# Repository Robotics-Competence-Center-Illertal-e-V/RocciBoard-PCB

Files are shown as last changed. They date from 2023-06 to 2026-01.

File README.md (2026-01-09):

# Rocci Board

# Features

* 4x DC Motor outputs a 3 A (motor driver with current limitation)
* 8 separate i2c channels
* low voltage shutdown for battery protection
* i2c fully protected against 12V and reverse polarity
* 3 A switching regulator for 5 V
* 3,3 V with 1 A LDO
* 8 V for Arduino VIN pin
* reverse polarity protection on battery connector
* short circuit protection on all supply pins

# Schematic

[Schematic as pdf](documentation/RocciBoard.pdf)

[Layout as pdf](documentation/RocciBoard__Assembly.pdf)

# Pinout Diagram

## Top

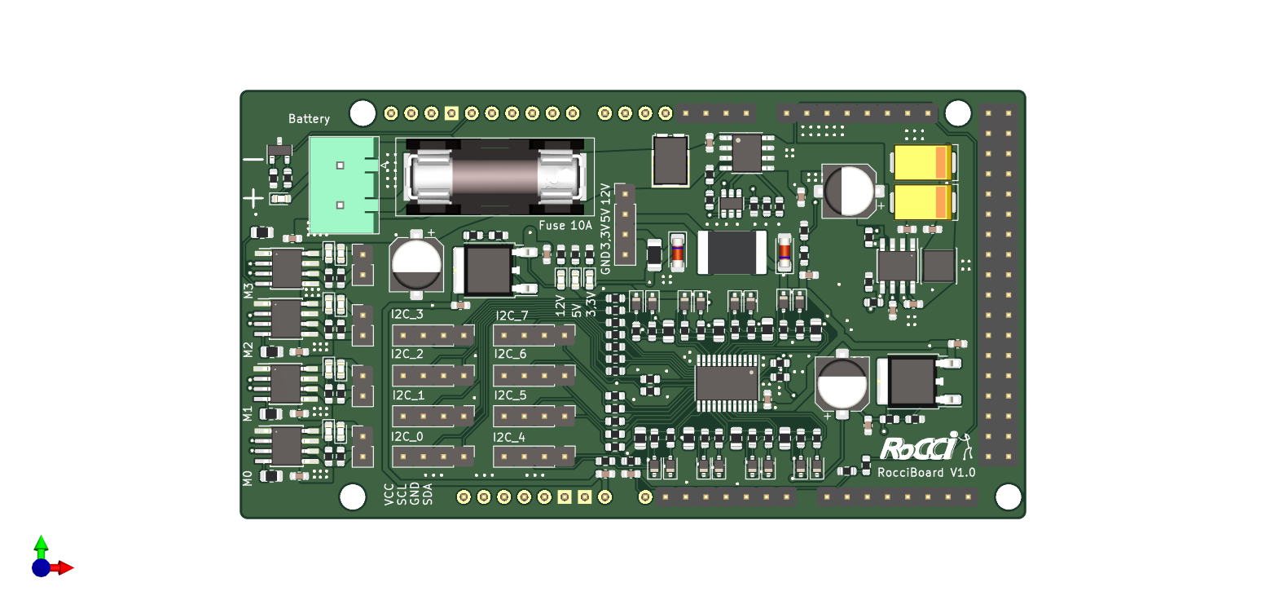
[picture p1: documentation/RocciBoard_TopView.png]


## Bottom

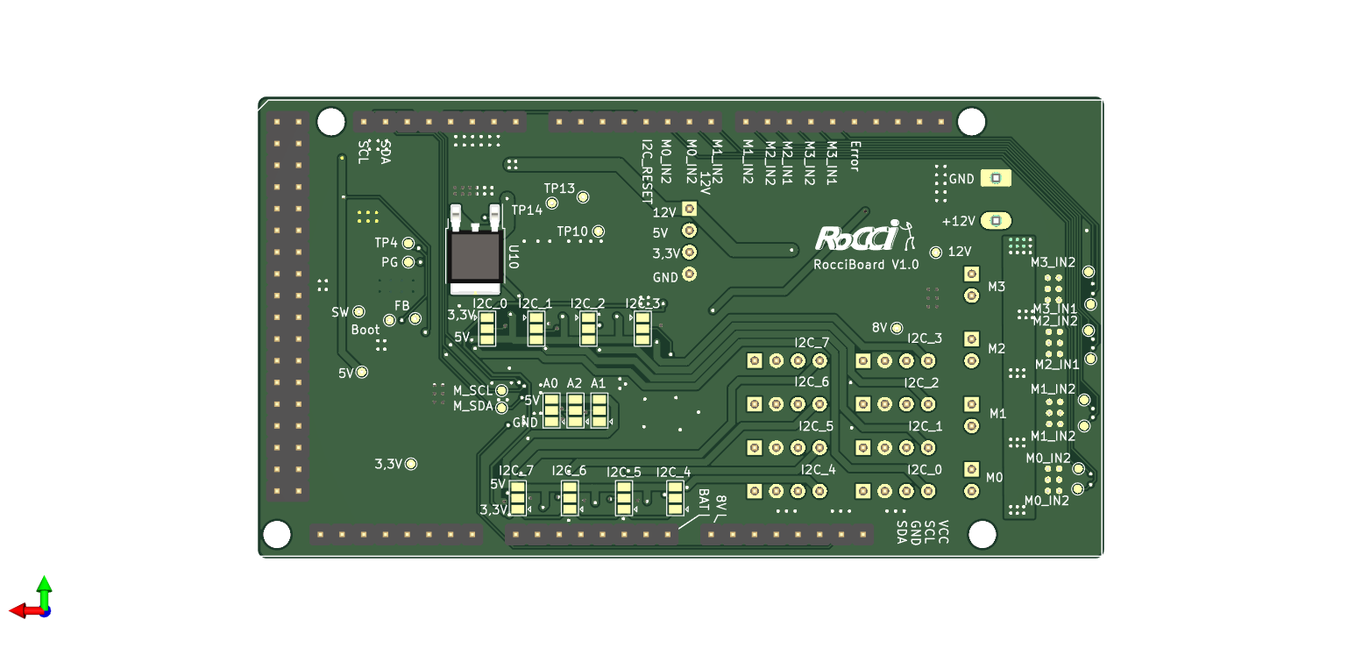
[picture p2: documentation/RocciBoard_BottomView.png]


## Hand Assembled Components

male pinheader with femal back:
1* 4
1* 7
2* 8
1* 18x2

male pinheader:
1* 8
1* 10
1* 4
1* 1
9* 4
4* 2

1* XT60 Male

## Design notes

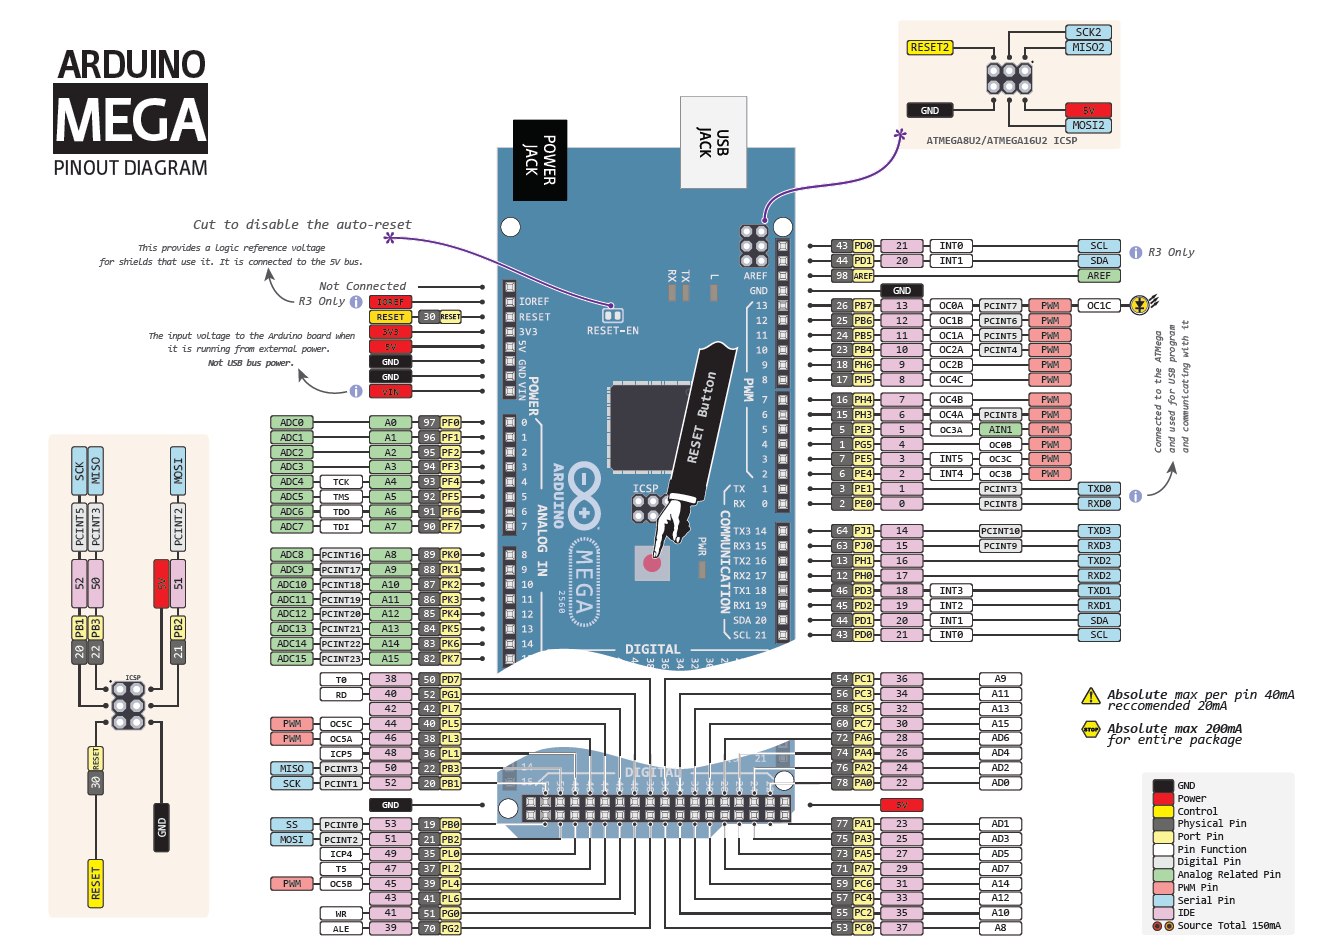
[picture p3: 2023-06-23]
datasheets/ARDUINO-Mega-Pinout-Diagram.png

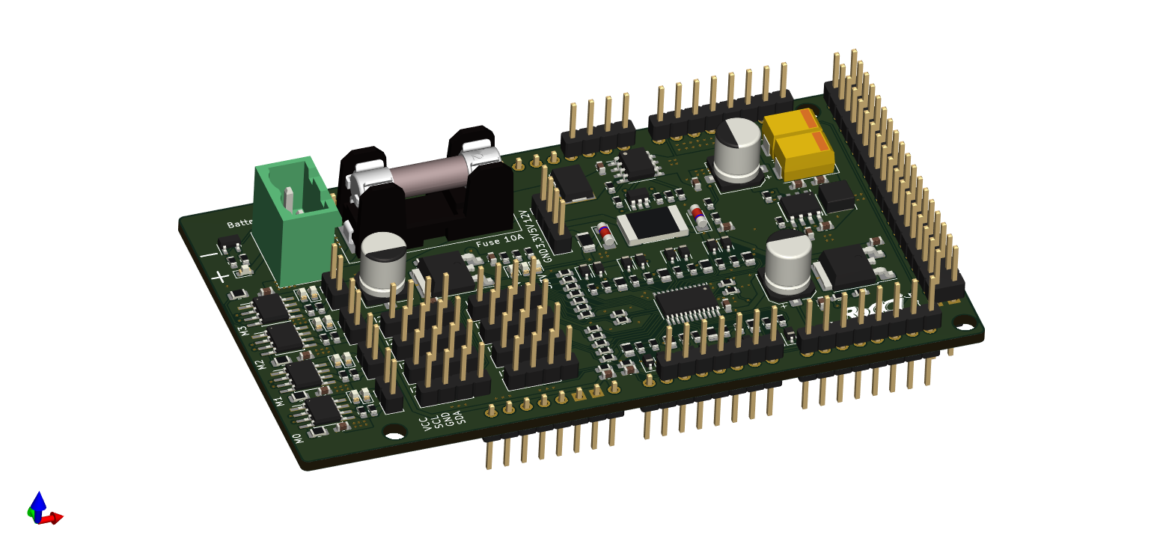
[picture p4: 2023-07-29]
documentation/RocciBoard_3DView.png

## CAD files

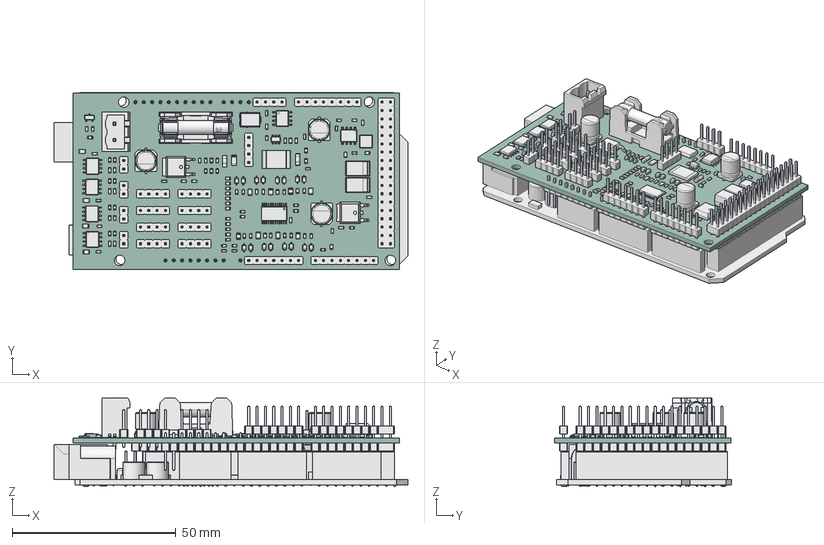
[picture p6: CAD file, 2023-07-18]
3d_model/board_arduino_assembly.FCStd
108.0 x 54.0 x 27.0 mm
ArduinoMega_STEP_AP203
RocciShield PCB

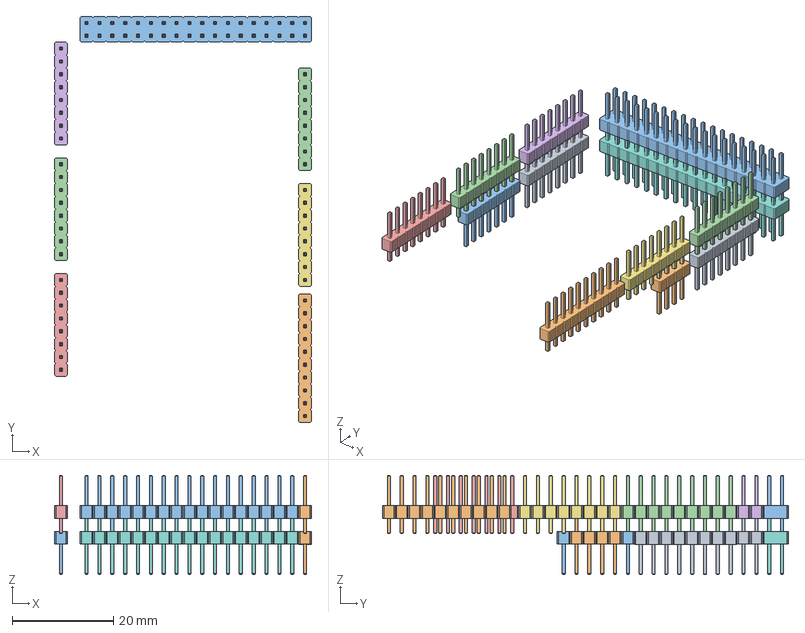
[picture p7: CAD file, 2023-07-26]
custom_parts/3d_shield_connector.FCStd
50.8 x 80.3 x 19.6 mm
PinHeader_1x08_P254mm_Vertical
PinHeader_1x10_P254mm_Vertical
PinHeader_2x18_P254mm_Vertical
PinHeader_1x08_P254mm_Vertical001
PinHeader_1x08_P254mm_Vertical002
PinHeader_1x08_P254mm_Vertical003
PinHeader_1x08_P254mm_Vertical004
PinHeader_2x18_P254mm_Vertical001
PinHeader_1x08_P254mm_Vertical005
PinHeader_1x04_P254mm_Vertical
PinHeader_1x07_P254mm_Vertical
PinHeader_1x08_P254mm_Vertical006

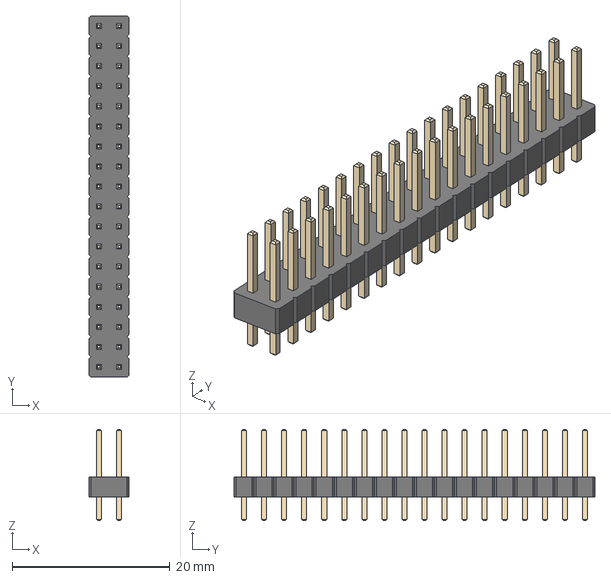
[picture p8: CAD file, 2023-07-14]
external_libs/PinHeader_2x18_P2.54mm_Vertical.step
5.08 x 45.7 x 11.5 mm

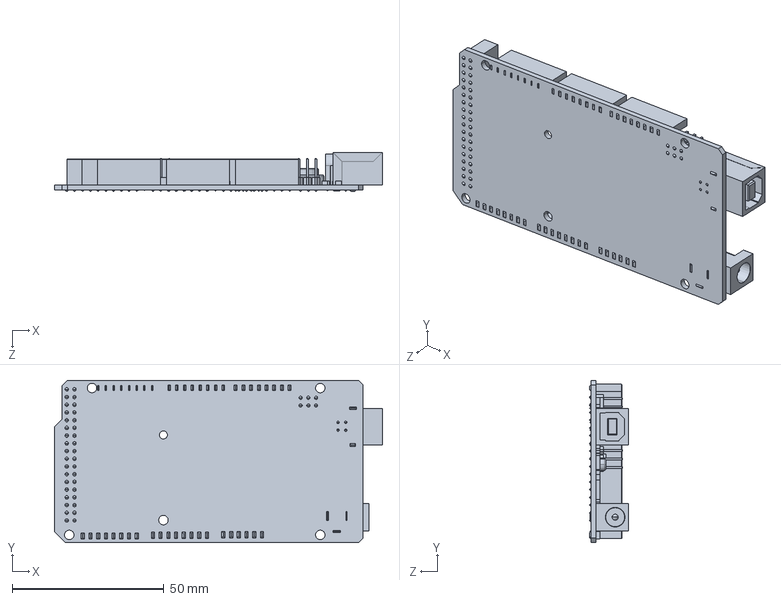
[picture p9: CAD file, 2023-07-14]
3d_model/ArduinoMega_STEP_AP203.STEP
107.9 x 53.4 x 13.0 mm

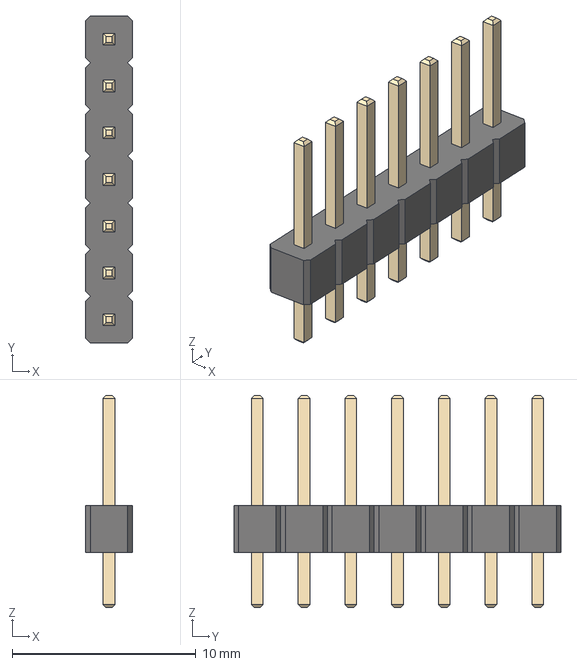
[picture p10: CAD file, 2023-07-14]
external_libs/PinHeader_1x07_P2.54mm_Vertical.step
2.54 x 17.8 x 11.5 mm

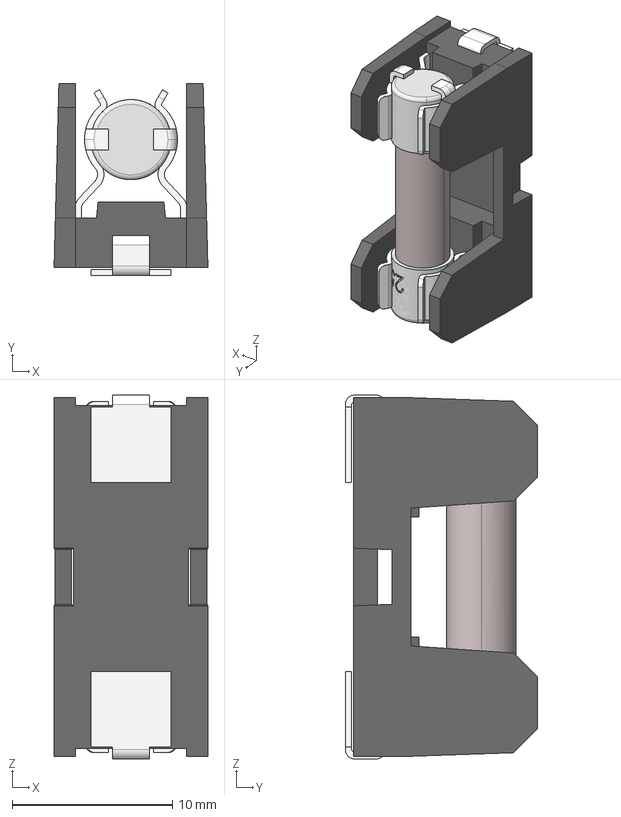
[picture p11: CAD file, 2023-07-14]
external_libs/Fuse Holders SMD 5x20mm + Fuse.stp
9.60 x 12.0 x 22.7 mm

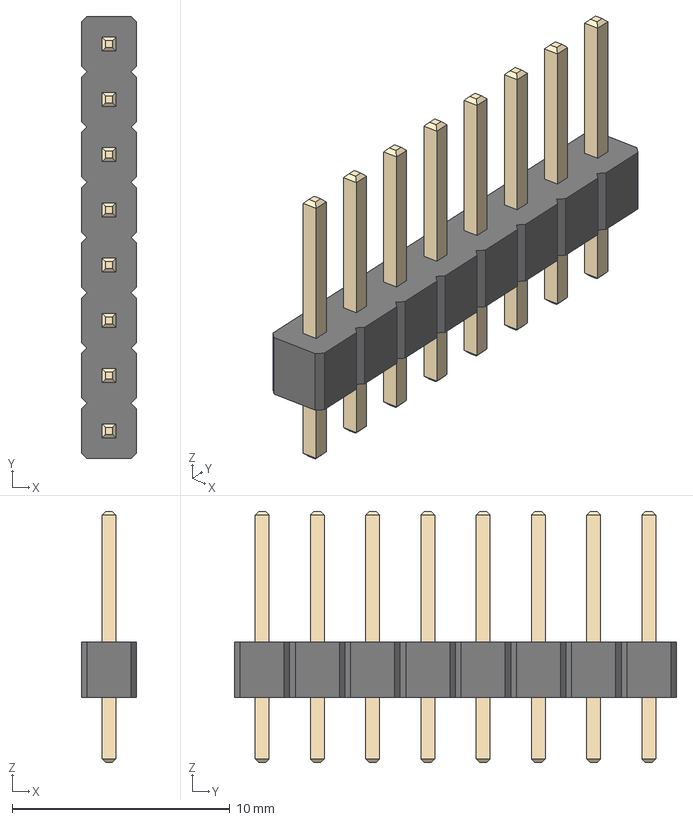
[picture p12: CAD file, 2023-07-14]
external_libs/PinHeader_1x08_P2.54mm_Vertical.step
2.54 x 20.3 x 11.5 mm

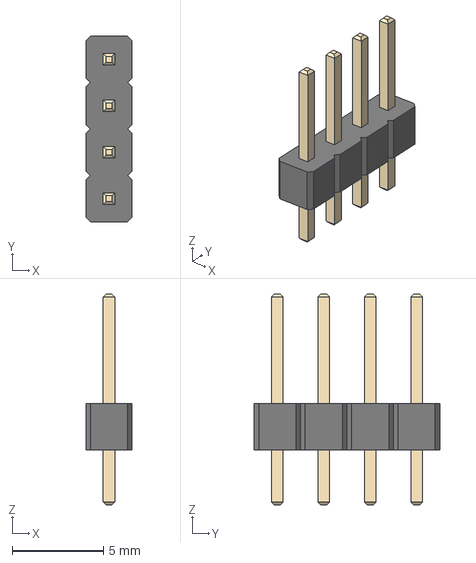
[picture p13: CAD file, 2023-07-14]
external_libs/PinHeader_1x04_P2.54mm_Vertical.step
2.54 x 10.2 x 11.5 mm

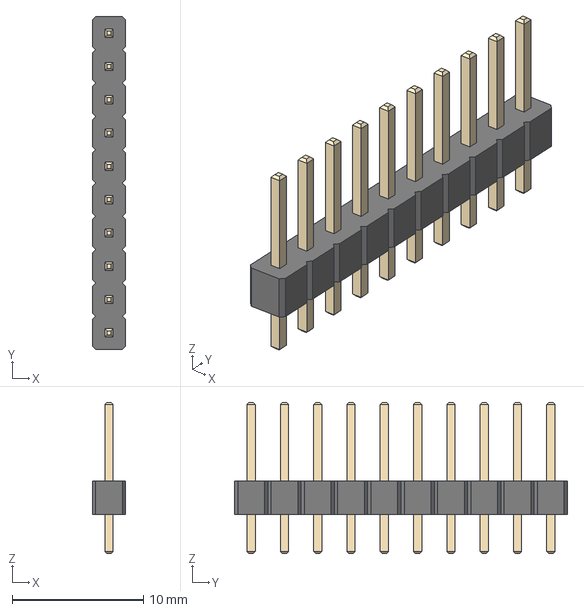
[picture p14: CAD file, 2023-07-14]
external_libs/PinHeader_1x10_P2.54mm_Vertical.step
2.54 x 25.4 x 11.5 mm

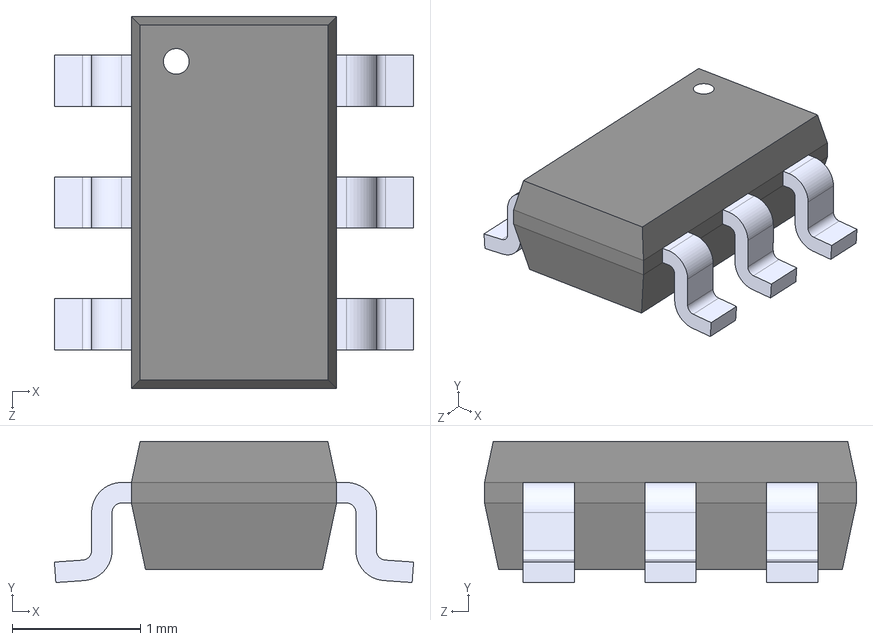
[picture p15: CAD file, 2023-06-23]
external_libs/TPS3700DDCR.step
2.80 x 1.10 x 2.90 mm

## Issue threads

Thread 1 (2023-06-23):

Verbesserungen/Vorschläge 1

JonasBiener, 2023-06-23:
- Für jedes Spannungslevel eine Power-On-LED, damit man jedes Netz einzeln sehen kann
- Rote Error-LED auf einen Digital-Pin, damit man harte Softwarefehler (I²C, Sensor, etc.)ausgeben kann (primär für die Library gedacht). Die LED sollte dann am Besten auch im sichtbaren Bereich der Platine liegen.

Closed 2023-06-24.

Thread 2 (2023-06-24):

Verbesserungen/Vorschläge 2

JonasBiener, 2023-06-24:
_@teeheee Ich sehe, dass die Platine immer mehr Fortschritte macht. Danke auf jedenfall für dein Engagement!_

**Ich habe noch ein paar weitere Fragen, bzw. Vorschläge:**

- Welche Art von Sicherung sind für die I²C-Busses vorgesehen (also F1 + F3-F25)?
- Sind die 5V des DC-DC-Wandlers glatt (bzw. die Frequenz hoch) genug, dass es keine Probleme macht? Oder geht man da auf 5.5V und packt noch einen linearen Spannungsregler zwischen rein?
- Wie wird der Vorwiderstand der Motor-Richtungsanzeigen bemessen? Würde da nicht knapp die Hälfte reichen?
- 10,8V als Abschaltspannung finde ich etwas hoch, wir mussten zeitbedingt (und v.a. um den Pi nicht immer zu rebooten) unsere Akkus wesentlich tiefer entladen. 3S-LiPos nehmen meines Wissens nach erst ab 9.9V Schaden, daher würde ich eine Not-Abschaltung (die ja wirklich nur zum Schutz der Hardware da ist) bei ca. 10.2V ansetzen. Eine Software-Warnung (die weichere Methode, vor allem im Spiel / Lauf) kann ja dann über den ADC implementiert werden.

Closed 2023-06-27.

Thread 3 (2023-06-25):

ADC-Akkuspannungsmessung

JonasBiener, 2023-06-25:
Die aktuelle Variante der Akku-Spannungsmessung über den Cutoff-Spannungswandler teilt den Bereich der Akkuspannung (10.2-12.6V) in einen Bereich von 0.40-0.50V. Das entspricht beim Arduino 5V-ADC gerade einmal 20 Werten.
Damit diese Auflösung vergrößert wird, empfehle ich einen separaten Spannungsteiler nur für den ADC.

Als Widerstandswerte bieten sich **287k 1%** (zu 12V) und **100k 1%** (zu GND) an. Damit liegt die Spannung in einem Bereich von 1,64-3,26V und es stehen 126 Werte beim 5V-ADC zur Verfügung (beim 3.3V-ADC sind es natürlich mehr).

Die softwareseitige Implementierung ist übrigens auch mit den verschiedenen ADCs möglich, weil über Precompiler-Directives eine separate Implementierung für AVR- und ARM-Boards möglich ist.

Closed 2023-06-27.

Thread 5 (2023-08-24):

Error LED Q2 Source<->Drain vertauscht

teeheee, 2023-08-24:
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

Closed 2023-09-29.

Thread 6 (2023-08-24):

1k Resistor has wrong component in BOM (LCSL part number)

teeheee, 2023-08-24:
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

Closed 2023-09-29.

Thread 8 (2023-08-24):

prevent backcurrent from Arduino USB to the rest of the board

teeheee, 2023-08-24:
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

Closed 2023-09-29.

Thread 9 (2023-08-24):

OVP 12V<->5V short circuit does not work

teeheee, 2023-08-24:
solution: 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

teeheee, 2023-08-31:
Habs nicht hinbekommen, dass es richtig funktionierrt.

Nächster versuch wäre folgende Schaltung: https://de.wikipedia.org/wiki/Klemmschaltung_(Stromversorgung)

teeheee, 2023-08-31:
Triac: BT137S-600E
Sens: TL431

Set to 3,4 V and 5,1 V

At 8 A and 63 A peak the Triac should be enough to blow the fuse.

Maybe use one triac to blow the 12V fuse?

Should be enough to blow the 12V fuse

teeheee, 2023-09-29:
This circuit works as an attachment to the V1 board

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

Triac: BT137S-600E
Sens: TL431

Closed 2023-09-29.

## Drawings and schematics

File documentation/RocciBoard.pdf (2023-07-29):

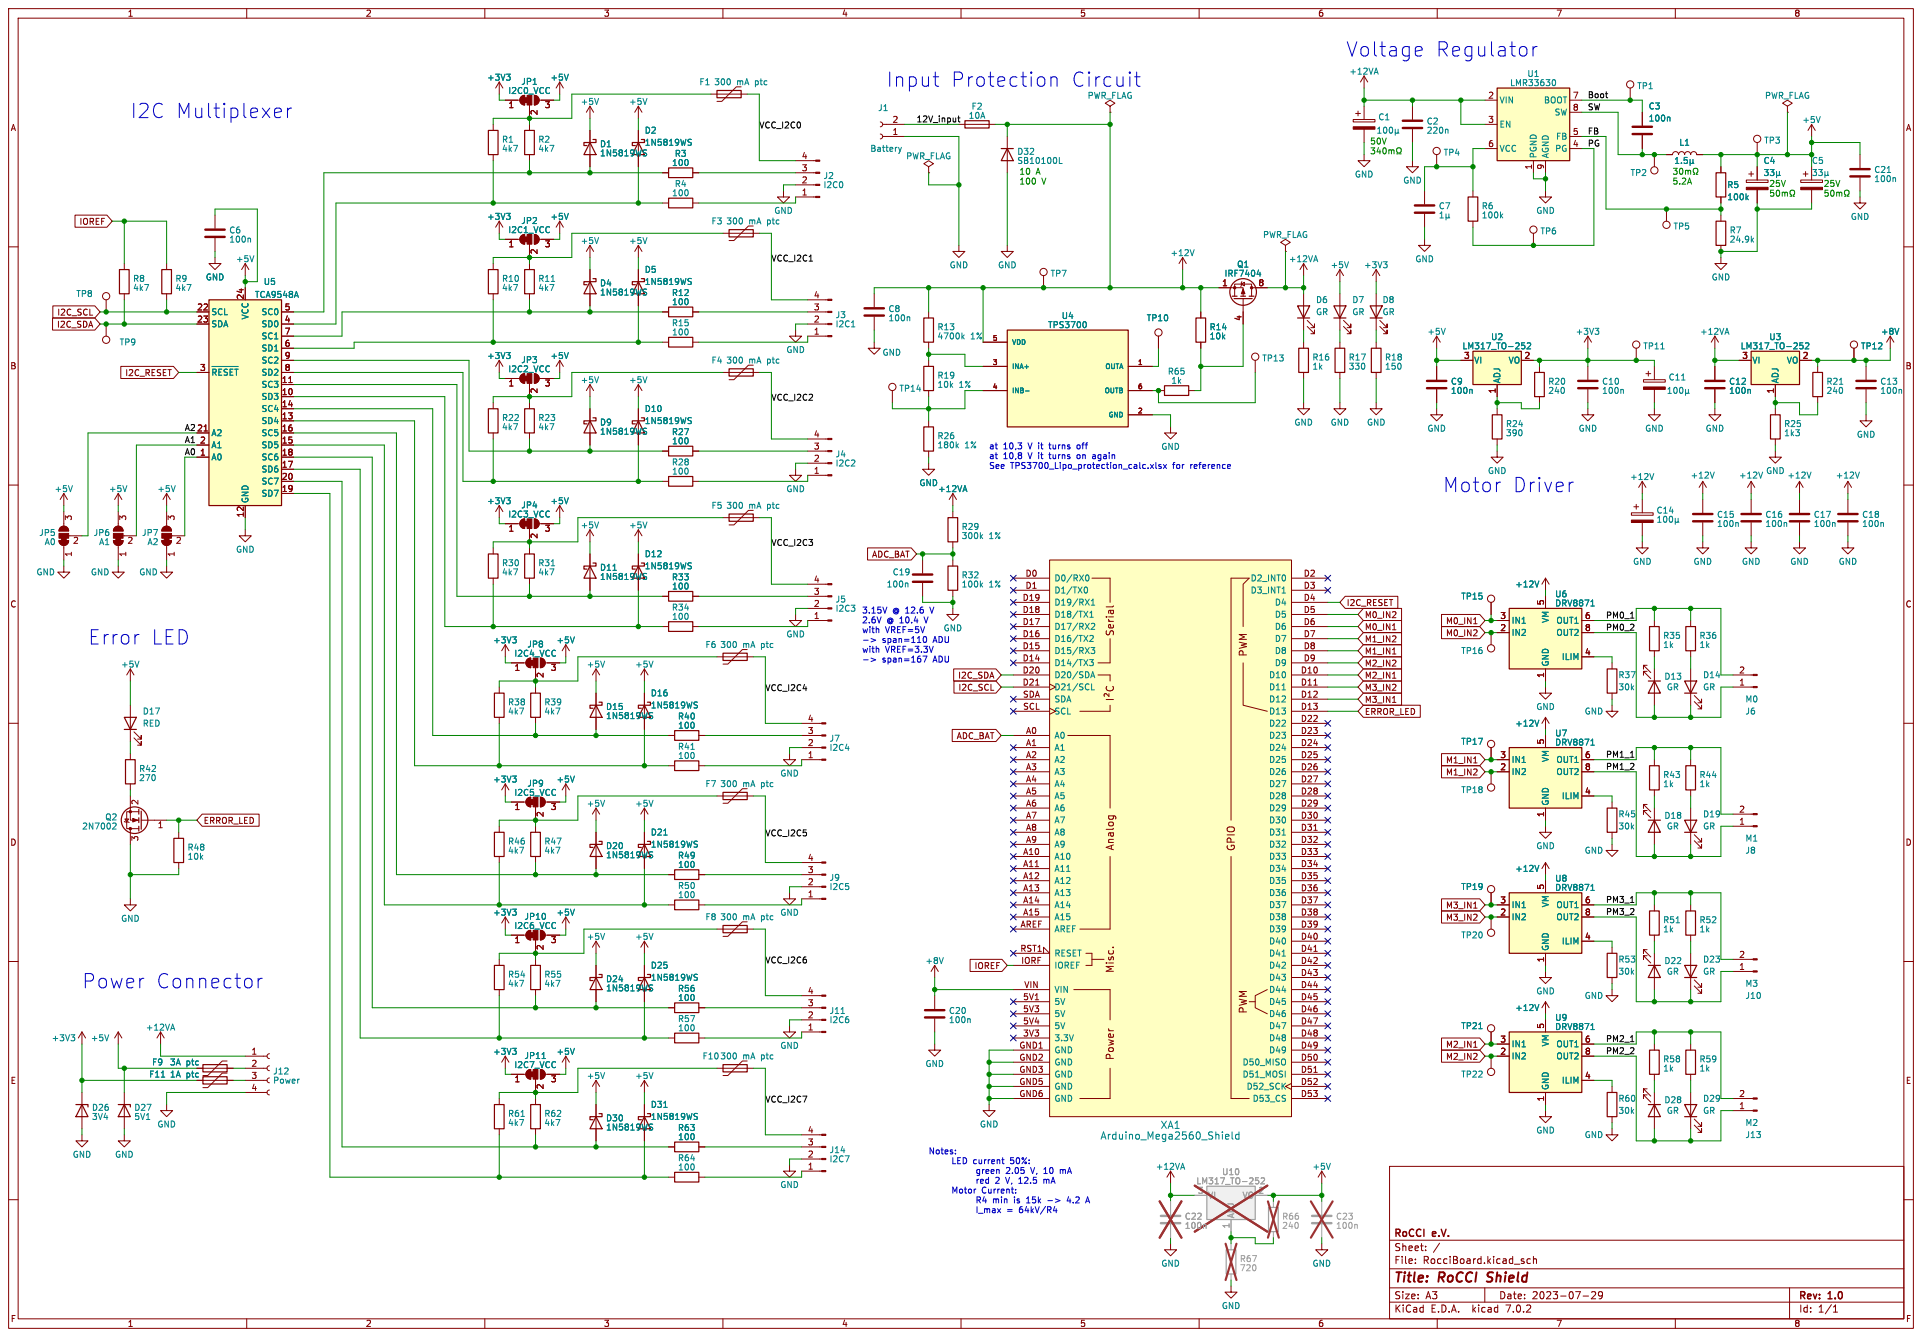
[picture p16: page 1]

1 VIN 2 EN 3 PG 4 FB 5 VCC 6 BOOT 7 SW 8 AGND

Id: 1/1 Title: RoCCI Shield

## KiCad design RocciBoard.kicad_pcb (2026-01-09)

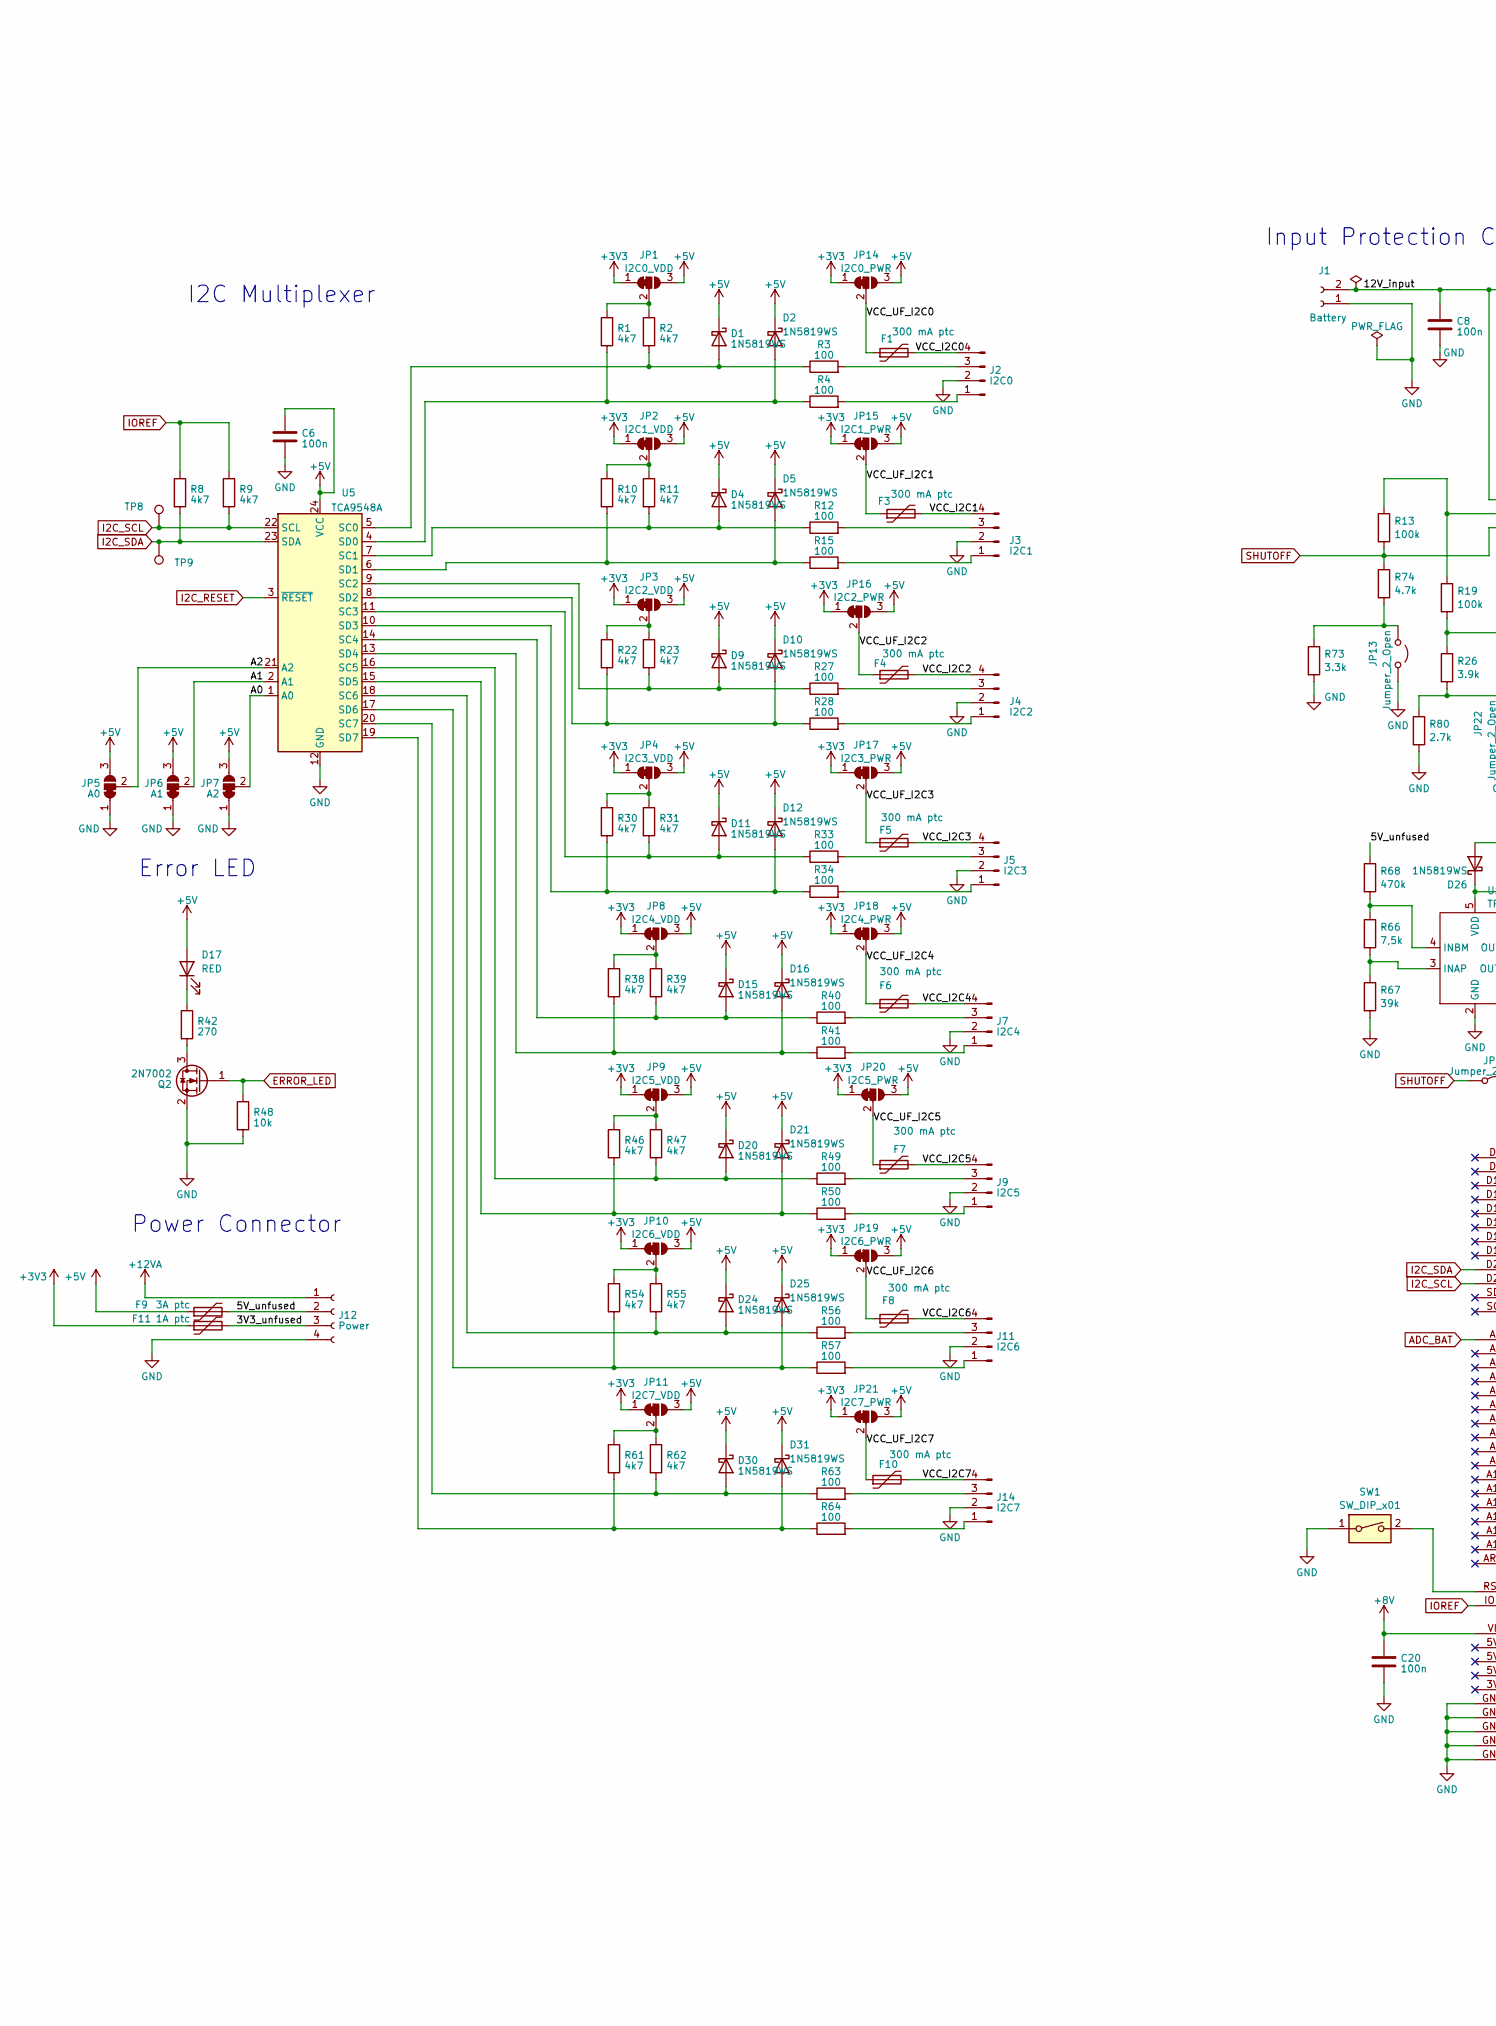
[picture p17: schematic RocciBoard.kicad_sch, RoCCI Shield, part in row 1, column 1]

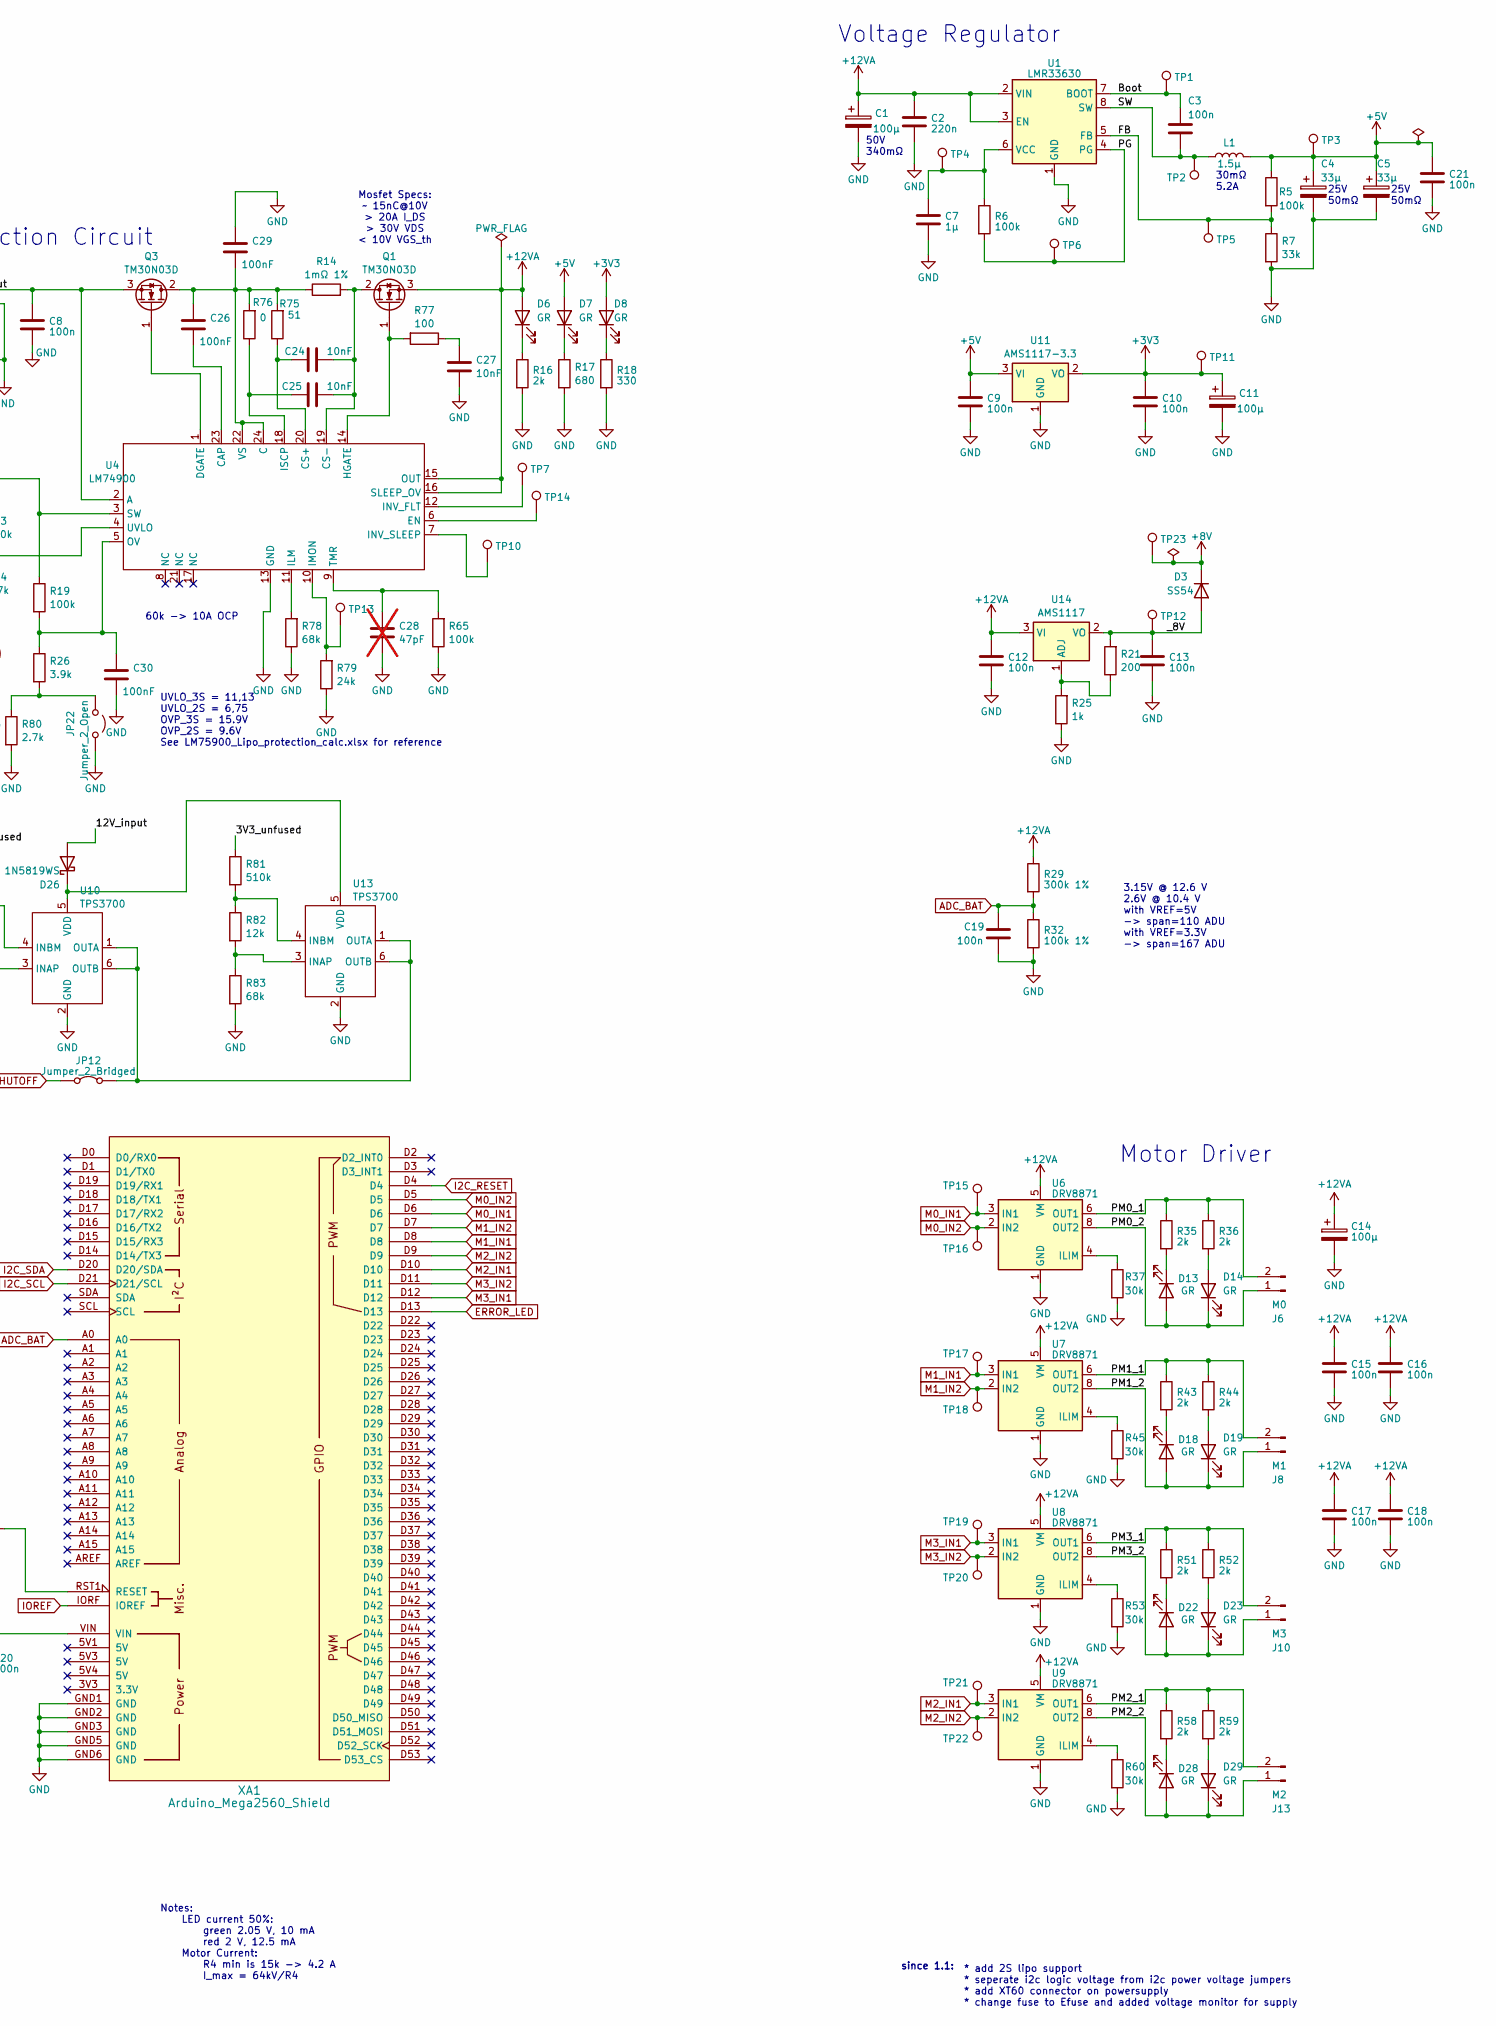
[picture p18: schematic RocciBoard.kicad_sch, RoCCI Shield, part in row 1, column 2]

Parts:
C1, C11, C14: 100µ; CP_Elec_6.3x7.7; LCSC C962164
C2: 220n; C_0603_1608Metric; LCSC C21120
C3, C6, C8, C9, C10, C12, C13, C15, C16, C17, C18, C19, C20, C21: 100n; C_0603_1608Metric; LCSC C14663
C4, C5: 33µ; CP_EIA-7343-43_Kemet-X; LCSC C212716
C7: 1µ; C_0603_1608Metric; LCSC C15849
C24, C25, C27: 10nF; C_0603_1608Metric; LCSC C57112
C26, C29, C30: 100nF; C_0603_1608Metric; LCSC C14663
C28: 47pF; C_0603_1608Metric; LCSC C1671; not fitted
D1, D2, D4, D5, D9, D10, D11, D12, D15, D16, D20, D21, D24, D25, D26, D30, D31: 1N5819WS; D_SOD-323; LCSC C191023
D3: SS54; D_SMA; LCSC C22452
D6, D7, D8, D13, D14, D18, D19, D22, D23, D28, D29: GR; LED_0603_1608Metric; LCSC C965805
D17: RED; LED_0603_1608Metric; LCSC C2286
F1, F3, F4, F5, F6, F7, F8, F10: 300 mA ptc; Fuse_0805_2012Metric; LCSC C261938
F9: 3A ptc; Fuse_2920_7451Metric; LCSC C2977527
F11: 1A ptc; Fuse_1206_3216Metric; LCSC C910830
J1: Battery; AMASS_XT60-M_1x02_P7.20mm_Vertical
J2: I2C0; PinHeader_1x04_P2.54mm_Vertical
J3: I2C1; PinHeader_1x04_P2.54mm_Vertical
J4: I2C2; PinHeader_1x04_P2.54mm_Vertical
J5: I2C3; PinHeader_1x04_P2.54mm_Vertical
J6: M0; PinHeader_1x02_P2.54mm_Vertical
J7: I2C4; PinHeader_1x04_P2.54mm_Vertical
J8: M1; PinHeader_1x02_P2.54mm_Vertical
J9: I2C5; PinHeader_1x04_P2.54mm_Vertical
J10: M3; PinHeader_1x02_P2.54mm_Vertical
J11: I2C6; PinHeader_1x04_P2.54mm_Vertical
J12: Power; PinHeader_1x04_P2.54mm_Vertical
J13: M2; PinHeader_1x02_P2.54mm_Vertical
J14: I2C7; PinHeader_1x04_P2.54mm_Vertical
JP1: I2C0_VDD; SolderJumper-3_P1.3mm_Open_Pad1.0x1.5mm
JP2: I2C1_VDD; SolderJumper-3_P1.3mm_Open_Pad1.0x1.5mm
JP3: I2C2_VDD; SolderJumper-3_P1.3mm_Open_Pad1.0x1.5mm
JP4: I2C3_VDD; SolderJumper-3_P1.3mm_Open_Pad1.0x1.5mm
JP5: A0; SolderJumper-3_P1.3mm_Open_Pad1.0x1.5mm
JP6: A1; SolderJumper-3_P1.3mm_Open_Pad1.0x1.5mm
JP7: A2; SolderJumper-3_P1.3mm_Open_Pad1.0x1.5mm
JP8: I2C4_VDD; SolderJumper-3_P1.3mm_Open_Pad1.0x1.5mm
JP9: I2C5_VDD; SolderJumper-3_P1.3mm_Open_Pad1.0x1.5mm
JP10: I2C6_VDD; SolderJumper-3_P1.3mm_Open_Pad1.0x1.5mm
JP11: I2C7_VDD; SolderJumper-3_P1.3mm_Open_Pad1.0x1.5mm
JP12: Jumper_2_Bridged; SolderJumper-2_P1.3mm_Open_Pad1.0x1.5mm
JP13, JP22: Jumper_2_Open; SolderJumper-2_P1.3mm_Open_Pad1.0x1.5mm
JP14: I2C0_PWR; SolderJumper-3_P1.3mm_Open_Pad1.0x1.5mm
JP15: I2C1_PWR; SolderJumper-3_P1.3mm_Open_Pad1.0x1.5mm
JP16: I2C2_PWR; SolderJumper-3_P1.3mm_Open_Pad1.0x1.5mm
JP17: I2C3_PWR; SolderJumper-3_P1.3mm_Open_Pad1.0x1.5mm
JP18: I2C4_PWR; SolderJumper-3_P1.3mm_Open_Pad1.0x1.5mm
JP19: I2C6_PWR; SolderJumper-3_P1.3mm_Open_Pad1.0x1.5mm
JP20: I2C5_PWR; SolderJumper-3_P1.3mm_Open_Pad1.0x1.5mm
JP21: I2C7_PWR; SolderJumper-3_P1.3mm_Open_Pad1.0x1.5mm
L1: 1.5µ; L_Sunlord_SWPA4020S; LCSC C98360
Q1, Q3: TM30N03D; TO-252-2; LCSC C18186756
Q2: 2N7002; SOT-23; LCSC C8545
R1, R2, R8, R9, R10, R11, R22, R23, R30, R31, R38, R39, R46, R47, R54, R55, R61, R62: 4k7; R_0603_1608Metric; LCSC C23162
R3, R4, R12, R15, R27, R28, R33, R34, R40, R41, R49, R50, R56, R57, R63, R64, R77: 100; R_0603_1608Metric; LCSC C22775
R5, R6, R13, R19, R65: 100k; R_0603_1608Metric; LCSC C25803
R7: 33k; R_0603_1608Metric; LCSC C4216
R14: 1mΩ 1%; R_1206_3216Metric; LCSC C7467246
R16, R35, R36, R43, R44, R51, R52, R58, R59: 2k; R_0603_1608Metric; LCSC C22975
R17: 680; R_0603_1608Metric; LCSC C23228
R18: 330; R_0603_1608Metric; LCSC C23138
R21: 200; R_0603_1608Metric; LCSC C8218
R25: 1k; R_0603_1608Metric; LCSC C21190
R26: 3.9k; R_0603_1608Metric; LCSC C23018
R29: 300k 1%; R_0603_1608Metric; LCSC C23024
R32: 100k 1%; R_0603_1608Metric; LCSC C25803
R37, R45, R53, R60: 30k; R_0805_2012Metric; LCSC C22984
R42: 270; R_0603_1608Metric; LCSC C22966
R48: 10k; R_0603_1608Metric; LCSC C25804
R66: 7,5k; R_0603_1608Metric; LCSC C23234
R67: 39k; R_0603_1608Metric; LCSC C23153
R68: 470k; R_0603_1608Metric; LCSC C23178
R73: 3.3k; R_0603_1608Metric; LCSC C22978
R74: 4.7k; R_0603_1608Metric; LCSC C23162
R75: 51; R_0603_1608Metric; LCSC C23197
R76: 0; R_0603_1608Metric; LCSC C21189
R78, R83: 68k; R_0603_1608Metric; LCSC C23231
R79: 24k; R_0603_1608Metric; LCSC C23352
R80: 2.7k; R_0603_1608Metric; LCSC C13167
R81: 510k; R_0603_1608Metric; LCSC C23192
R82: 12k; R_0603_1608Metric; LCSC C22790
SW1: SW_DIP_x01; SW_Push_1P1T_XKB_TS-1187A; LCSC C318884
TP1, TP2, TP3, TP4, TP5, TP6, TP7, TP8, TP9, TP10, TP11, TP12, TP13, TP14, TP15, TP16, TP17, TP18, TP19, TP20, TP21, TP22, TP23: TestPoint_Pad_D1.0mm
U1: LMR33630; Texas_HSOP-8-1EP_3.9x4.9mm_P1.27mm_ThermalVias; LCSC C841384
U4: LM74900; VQFN-24-1EP_4x4mm_P0.5mm_EP2.5x2.5mm_ThermalVias; LCSC C20345498
U5: TCA9548A; TSSOP-24_4.4x7.8mm_P0.65mm; LCSC C130026
U6, U7, U8, U9: DRV8871; Texas_HTSOP-8-1EP_3.9x4.9mm_P1.27mm_EP2.95x4.9mm_Mask2.4x3.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; LCSC C75864
U10, U13: TPS3700; SOT-23-6; LCSC C33002
U11: AMS1117-3.3; SOT-223-3_TabPin2; LCSC C6186
U14: AMS1117; SOT-223-3_TabPin2; LCSC C347224
XA1: Arduino_Mega2560_Shield; Arduino_Mega2560_custom_Shield

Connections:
+3V3: C10.1, C11.1, D8.2 (A), F11.1, JP1.1 (A), JP2.1 (A), JP3.1 (A), JP4.1 (A), JP8.1 (A), JP9.1 (A), JP10.1 (A), JP11.1 (A), JP14.1 (A), JP15.1 (A), JP16.1 (A), JP17.1 (A), JP18.1 (A), JP19.1 (A), JP20.1 (A), JP21.1 (A), TP11.1, U11.2 (VO)
+5V: C4.1, C5.1, C6.1, C9.1, C21.1, D1.1 (K), D2.1 (K), D4.1 (K), D5.1 (K), D7.2 (A), D9.1 (K), D10.1 (K), D11.1 (K), D12.1 (K), D15.1 (K), D16.1 (K), D17.2 (A), D20.1 (K), D21.1 (K), D24.1 (K), D25.1 (K), D30.1 (K), D31.1 (K), F9.1, JP1.3 (B), JP2.3 (B), JP3.3 (B), JP4.3 (B), JP5.3 (B), JP6.3 (B), JP7.3 (B), JP8.3 (B), JP9.3 (B), JP10.3 (B), JP11.3 (B), JP14.3 (B), JP15.3 (B), JP16.3 (B), JP17.3 (B), JP18.3 (B), JP19.3 (B), JP20.3 (B), JP21.3 (B), L1.2, R5.1, TP3.1, U5.24 (VCC), U11.3 (VI)
+8V: C20.1, D3.1 (K), TP23.1, XA1.VIN
+12VA: C1.1, C2.1, C12.1, C14.1, C15.1, C16.1, C17.1, C18.1, D6.2 (A), J12.1, Q1.3 (S), R29.1, U1.2 (VIN), U1.3 (EN), U4.15 (OUT), U4.16 (SLEEP_OV), U6.5 (VM), U7.5 (VM), U8.5 (VM), U9.5 (VM), U14.3 (VI)
/3V3_unfused: F11.2, J12.3, R81.1
/5V_unfused: F9.2, J12.2, R68.1
/12V_input: C8.1, D26.2 (A), J1.2, Q3.3 (S), U4.2 (A)
/A0: JP7.2 (C), U5.1 (A0)
/A1: JP6.2 (C), U5.2 (A1)
/A2: JP5.2 (C), U5.21 (A2)
/Boot: C3.1, TP1.1, U1.7 (BOOT)
/FB: R5.2, R7.1, TP5.1, U1.5 (FB)
/PG: R6.2, TP6.1, U1.4 (PG)
/PM0_1: J6.2, R35.1, R36.1, U6.6 (OUT1)
/PM0_2: D13.2 (A), D14.1 (K), J6.1, U6.8 (OUT2)
/PM1_1: J8.2, R43.1, R44.1, U7.6 (OUT1)
/PM1_2: D18.2 (A), D19.1 (K), J8.1, U7.8 (OUT2)
/PM2_1: J13.2, R58.1, R59.1, U9.6 (OUT1)
/PM2_2: D28.2 (A), D29.1 (K), J13.1, U9.8 (OUT2)
/PM3_1: J10.2, R51.1, R52.1, U8.6 (OUT1)
/PM3_2: D22.2 (A), D23.1 (K), J10.1, U8.8 (OUT2)
/SW: C3.2, L1.1, TP2.1, U1.8 (SW)
/VCC_I2C0: F1.2, J2.4
/VCC_I2C1: F3.2, J3.4
/VCC_I2C2: F4.2, J4.4
/VCC_I2C3: F5.2, J5.4
/VCC_I2C4: F6.2, J7.4
/VCC_I2C5: F7.2, J9.4
/VCC_I2C6: F8.2, J11.4
/VCC_I2C7: F10.2, J14.4
/VCC_UF_I2C0: F1.1, JP14.2 (C)
/VCC_UF_I2C1: F3.1, JP15.2 (C)
/VCC_UF_I2C2: F4.1, JP16.2 (C)
/VCC_UF_I2C3: F5.1, JP17.2 (C)
/VCC_UF_I2C4: F6.1, JP18.2 (C)
/VCC_UF_I2C5: F7.1, JP20.2 (C)
/VCC_UF_I2C6: F8.1, JP19.2 (C)
/VCC_UF_I2C7: F10.1, JP21.2 (C)
/_8V: C13.1, D3.2 (A), R21.2, TP12.1, U14.2 (VO)
ADC_BAT: C19.2, R29.2, R32.1, XA1.A0
ERROR_LED: Q2.1 (G), R48.1, XA1.D13
GND: C1.2, C2.2, C4.2, C5.2, C6.2, C7.2, C8.2, C9.2, C10.2, C11.2, C12.2, C13.2, C14.2, C15.2, C16.2, C17.2, C18.2, C19.1, C20.2, C21.2, C27.2, C28.2, C29.1, C30.2, J1.1, J2.2, J3.2, J4.2, J5.2, J7.2, J9.2, J11.2, J12.4, J14.2, JP5.1 (A), JP6.1 (A), JP7.1 (A), JP13.2 (B), JP22.2 (B), Q2.2 (S), R7.2, R16.2, R17.2, R18.2, R25.1, R32.2, R37.2, R45.2, R48.2, R53.2, R60.2, R65.1, R67.2, R73.2, R78.1, R79.1, R80.2, R83.2, SW1.1, U1.1 (GND), U1.9 (GND), U4.13 (GND), U5.12 (GND), U6.1 (GND), U6.7 (GND), U6.9 (GND), U7.1 (GND), U7.7 (GND), U7.9 (GND), U8.1 (GND), U8.7 (GND), U8.9 (GND), U9.1 (GND), U9.7 (GND), U9.9 (GND), U10.2 (GND), U11.1 (GND), U13.2 (GND), XA1.GND1 (GND), XA1.GND2 (GND), XA1.GND3 (GND), XA1.GND5 (GND), XA1.GND6 (GND)
I2C_RESET: U5.3 (~RESET), XA1.D4
I2C_SCL: R9.2, TP8.1, U5.22 (SCL), XA1.D21 (D21/SCL)
I2C_SDA: R8.2, TP9.1, U5.23 (SDA), XA1.D20 (D20/SDA)
IOREF: R8.1, R9.1, XA1.IORF (IOREF)
M0_IN1: TP15.1, U6.3 (IN1), XA1.D6
M0_IN2: TP16.1, U6.2 (IN2), XA1.D5
M1_IN1: TP17.1, U7.3 (IN1), XA1.D8
M1_IN2: TP18.1, U7.2 (IN2), XA1.D7
M2_IN1: TP21.1, U9.3 (IN1), XA1.D10
M2_IN2: TP22.1, U9.2 (IN2), XA1.D9
M3_IN1: TP19.1, U8.3 (IN1), XA1.D12
M3_IN2: TP20.1, U8.2 (IN2), XA1.D11
unnamed: C27.1, R77.1
unnamed: D1.2 (A), R2.2, R3.1, U5.5 (SC0)
unnamed: D2.2 (A), R1.2, R4.1, U5.4 (SD0)
unnamed: D4.2 (A), R11.2, R12.1, U5.7 (SC1)
unnamed: D5.2 (A), R10.2, R15.1, U5.6 (SD1)
unnamed: D6.1 (K), R16.1
unnamed: D7.1 (K), R17.1
unnamed: D8.1 (K), R18.1
unnamed: D9.2 (A), R23.2, R27.1, U5.9 (SC2)
unnamed: D10.2 (A), R22.2, R28.1, U5.8 (SD2)
unnamed: D11.2 (A), R31.2, R33.1, U5.11 (SC3)
unnamed: D12.2 (A), R30.2, R34.1, U5.10 (SD3)
unnamed: D13.1 (K), R35.2
unnamed: D14.2 (A), R36.2
unnamed: D15.2 (A), R39.2, R40.1, U5.14 (SC4)
unnamed: D16.2 (A), R38.2, R41.1, U5.13 (SD4)
unnamed: D17.1 (K), R42.1
unnamed: D18.1 (K), R43.2
unnamed: D19.2 (A), R44.2
unnamed: D20.2 (A), R47.2, R49.1, U5.16 (SC5)
unnamed: D21.2 (A), R46.2, R50.1, U5.15 (SD5)
unnamed: D22.1 (K), R51.2
unnamed: D23.2 (A), R52.2
unnamed: D24.2 (A), R55.2, R56.1, U5.18 (SC6)
unnamed: D25.2 (A), R54.2, R57.1, U5.17 (SD6)
unnamed: D26.1 (K), U10.5 (VDD), U13.5 (VDD)
unnamed: D28.1 (K), R58.2
unnamed: D29.2 (A), R59.2
unnamed: D30.2 (A), R62.2, R63.1, U5.20 (SC7)
unnamed: D31.2 (A), R61.2, R64.1, U5.19 (SD7)
unnamed: J2.1, R4.2
unnamed: J2.3, R3.2
unnamed: J3.1, R15.2
unnamed: J3.3, R12.2
unnamed: J4.1, R28.2
unnamed: J4.3, R27.2
unnamed: J5.1, R34.2
unnamed: J5.3, R33.2
unnamed: J7.1, R41.2
unnamed: J7.3, R40.2
unnamed: J9.1, R50.2
unnamed: J9.3, R49.2
unnamed: J11.1, R57.2
unnamed: J11.3, R56.2
unnamed: J14.1, R64.2
unnamed: J14.3, R63.2
unnamed: JP1.2 (C), R1.1, R2.1
unnamed: JP2.2 (C), R10.1, R11.1
unnamed: JP3.2 (C), R22.1, R23.1
unnamed: JP4.2 (C), R30.1, R31.1
unnamed: JP8.2 (C), R38.1, R39.1
unnamed: JP9.2 (C), R46.1, R47.1
unnamed: JP10.2 (C), R54.1, R55.1
unnamed: JP11.2 (C), R61.1, R62.1
unnamed: JP12.2 (B), U10.1 (OUTA), U10.6 (OUTB), U13.1 (OUTA), U13.6 (OUTB)
unnamed: JP13.1 (A), R73.1, R74.2
unnamed: JP22.1 (A), R26.2, R80.1
unnamed: C24.2, C25.2, Q1.2 (D), R14.2, U4.19 (CS-)
unnamed: Q1.1 (G), R77.2, U4.14 (HGATE)
unnamed: Q2.3 (D), R42.2
unnamed: C26.1, C29.2, Q3.2 (D), R14.1, R75.2, R76.2, U4.22 (VS), U4.24 (C)
unnamed: Q3.1 (G), U4.1 (DGATE)
unnamed: C7.1, R6.1, TP4.1, U1.6 (VCC)
unnamed: C26.2, U4.23 (CAP)
unnamed: C24.1, R75.1, U4.20 (CS+)
unnamed: TP14.1, U4.6 (EN)
unnamed: R78.2, U4.11 (ILM)
unnamed: R79.2, TP13.1, U4.10 (IMON)
unnamed: TP7.1, U4.12 (INV_FLT)
unnamed: TP10.1, U4.7 (INV_SLEEP)
unnamed: C25.1, R76.1, U4.18 (ISCP)
unnamed: C30.1, R19.2, R26.1, U4.5 (OV)
unnamed: R13.1, R19.1, U4.3 (SW)
unnamed: C28.1, R65.2, U4.9 (TMR)
unnamed: R37.1, U6.4 (ILIM)
unnamed: R45.1, U7.4 (ILIM)
unnamed: R53.1, U8.4 (ILIM)
unnamed: R60.1, U9.4 (ILIM)
unnamed: R66.2, R67.1, U10.3 (INAP)
unnamed: R66.1, R68.2, U10.4 (INBM)
unnamed: R82.2, R83.1, U13.3 (INAP)
unnamed: R81.2, R82.1, U13.4 (INBM)
unnamed: R21.1, R25.2, U14.1 (ADJ)
unnamed: SW1.2, XA1.RST1 (RESET)
SHUTOFF: JP12.1 (A), R13.2, R74.1, U4.4 (UVLO)

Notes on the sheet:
Notes: LED current 50%: green 2.05 V, 10 mA red 2 V, 12.5 mA Motor Current: R4 min is 15k -> 4.2 A I_max = 64kV/R4
Error LED
30mΩ 5.2A
Mosfet Specs: ~ 15nC@10V > 20A I_DS > 30V VDS < 10V VGS_th
3.15V @ 12.6 V 2.6V @ 10.4 V with VREF=5V -> span=110 ADU with VREF=3.3V -> span=167 ADU
Motor Driver
since 1.1:
50V 340mΩ
60k -> 10A OCP
UVLO_3S = 11,13 UVLO_2S = 6,75 OVP_3S = 15.9V OVP_2S = 9.6V See LM75900_Lipo_protection_calc.xlsx for reference
Input Protection Circuit
25V 50mΩ
I2C Multiplexer
Power Connector
* add 2S lipo support * seperate i2c logic voltage from i2c power voltage jumpers * add XT60 connector on powersupply * change fuse to Efuse and added voltage monitor for supply
Voltage Regulator

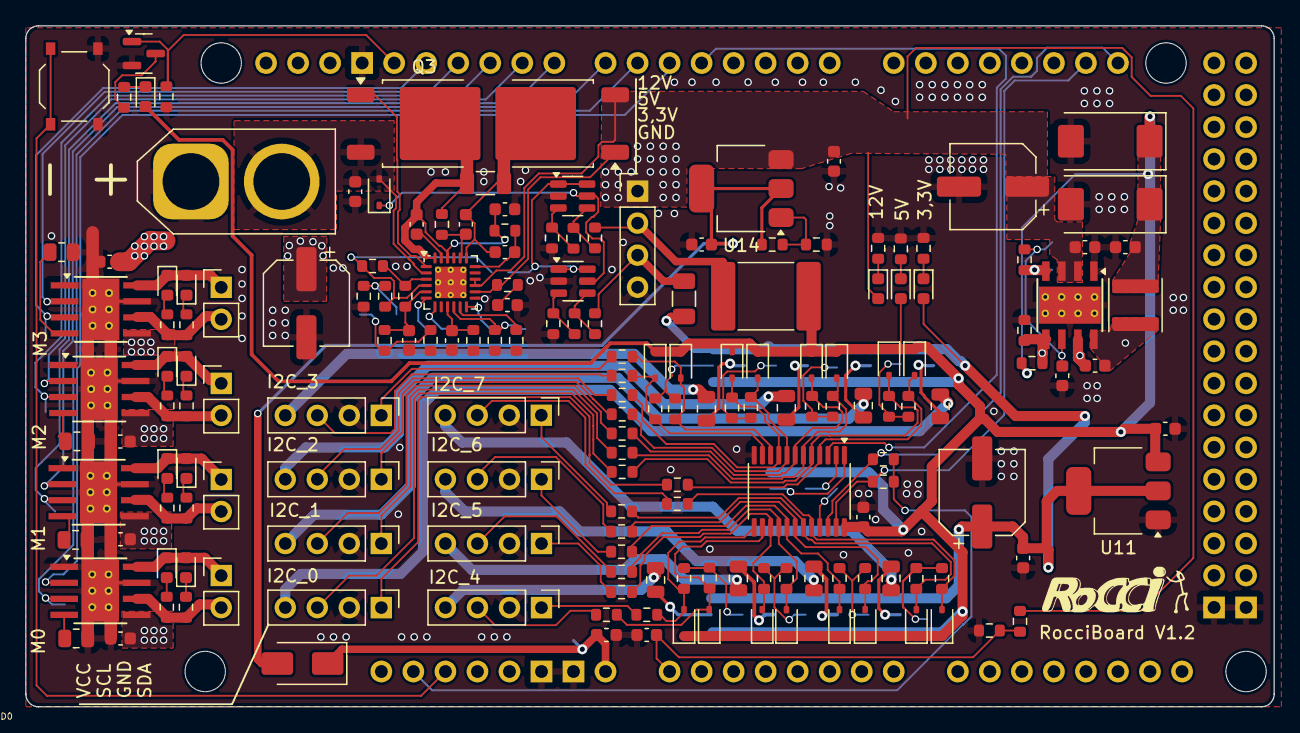
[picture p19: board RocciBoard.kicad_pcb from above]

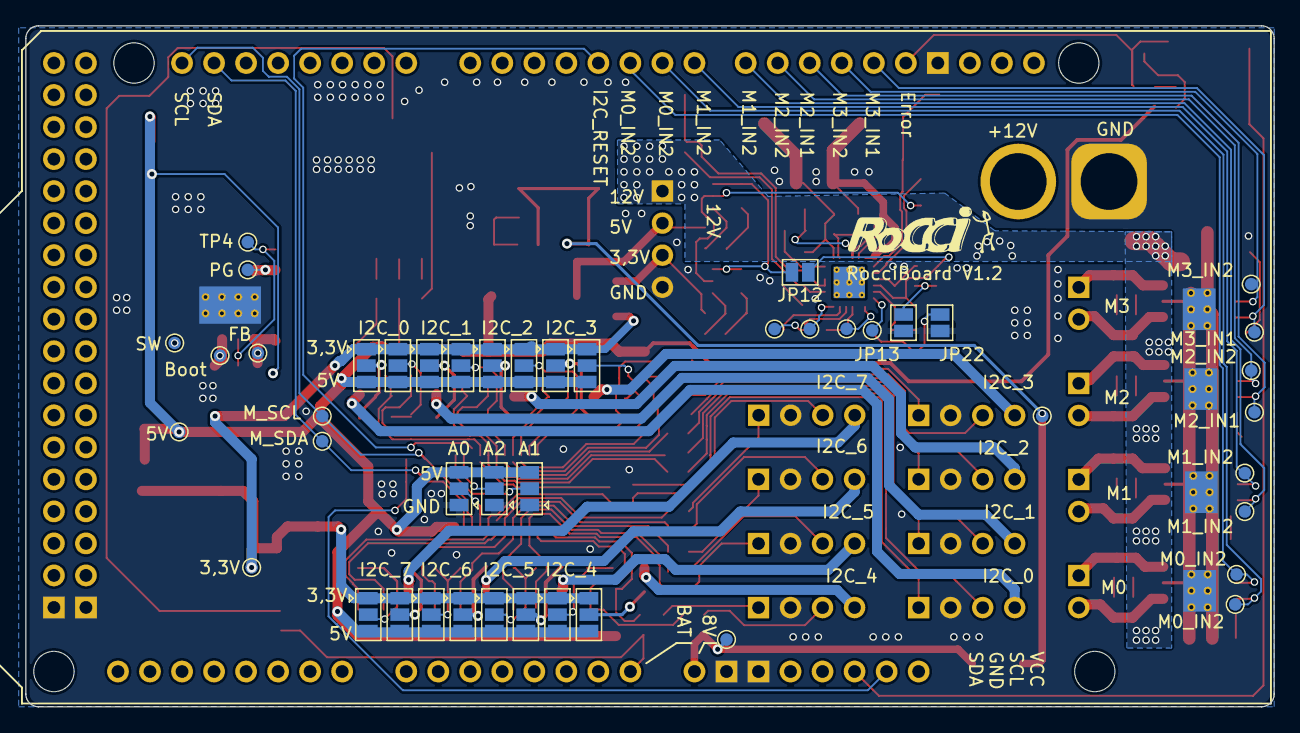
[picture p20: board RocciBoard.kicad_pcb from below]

Board: 2 copper layers, 99.0 x 54.0 mm, 221 parts (45 on the bottom side), 139 nets.

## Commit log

2023-06-23 first draft of schematic almost complete
    [RocciShield.kicad_pcb, RocciShield.kicad_sch]
2023-06-23 fixed issue #1 and some more things
    [RocciShield.kicad_sch, TPS3700DDCR.step]
2023-06-23 added zener diode
    [RocciShield.kicad_sch]
2023-06-24 changed pwm pins, added footprints, started JLPCB component selection
    [RocciShield.csv, RocciShield.kicad_pcb, RocciShield.kicad_sch]
2023-06-25 change linear regulator to lm317 (jlc basic part)
    [LMR336x0_calculator_A0.xlsx, RocciShield.kicad_pcb]
2023-06-26 added changes from #2
    [RocciShield.kicad_pcb, RocciShield.kicad_sch, TPS3700_Lipo_protection_calc.xlsx]
2023-06-27 finished JLCPCB selection and fixed isse #3
    [RocciShield.kicad_pcb, RocciShield.kicad_sch]
2023-06-29 added more TODOs
    [RocciShield.kicad_pcb, RocciShield.kicad_sch]
2023-07-01 first placment finished. Needs some adjustment
    [BOM-RocciShield.csv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]
2023-07-05 first finished routing. Needs some cleanup
    [RocciShield.kicad_pcb, RocciShield.kicad_sch]
2023-07-13 finsihed routing again
    [RocciShield.kicad_pcb, RocciShield.kicad_sch]
2023-07-14 finished silcreen and 3d files
    [3d_shield_connector.FCStd, ArduinoMega_STEP_AP203.STEP, Fuse Holders SMD 5x20mm + Fuse.stp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]
2023-07-18 layout ready for review
    [BOM-RocciShield.csv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]
2023-07-18 added some documenation update
    [ArduinoMega_STEP_AP203.STEP, board_arduino_assembly.FCStd]
2023-07-19 changed i2c order
    [RocciShield.kicad_pcb, RocciShield.kicad_sch]
2023-07-19 aligned components
    [RocciShield.kicad_pcb]
2023-07-19 renamed project file to RocciBoard
    [3d_shield_connector.FCStd, RocciBoard.kicad_pcb, RocciBoard.kicad_sch]
2023-07-19 finished #4 TODO list
    [BOM-RocciBoard.csv, BOM-RocciShield.csv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]
2023-07-26 lochraster ist fertig
    [3d_shield_connector.FCStd, Lochraster.kicad_pcb, Lochraster.kicad_sch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]
2023-07-26 remove unused pads
    [Lochraster.kicad_pcb]
2023-07-27 final version V1.0
    [BOM-Lochraster.csv, BOM-RocciBoard.csv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]
2023-07-29 V1.0 finished
    [RocciBoard.kicad_sch]
2023-09-29 patch issue #9 add crowbar circuit piggyback pcb
    [BOM-crowbar.csv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]
2023-09-29 fixed #6 1k LCSL part number was wrong
    [BOM-RocciBoard.csv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]
2023-09-29 fix #8 prevent backcurrent from Arduino USB
    [BOM-RocciBoard.csv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]
2023-09-29 fix #5 Error LED Q2 Source<->Drain vertauscht
    [RocciBoard-CuBottom.gbr, RocciBoard-CuTop.gbr, RocciBoard-EdgeCuts.gbr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]
2023-09-29 fix #7 all status LEDs are too bright
    [BOM-RocciBoard.csv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]
2023-09-29 fix #9 OVP 12V<->5V short circuit protection
    [BOM-RocciBoard.csv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]
2023-09-30 V 1.1
    [RocciBoard-CuBottom.gbr, RocciBoard-CuTop.gbr, RocciBoard-EdgeCuts.gbr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]
2024-09-01 fix #13 #12 #11 #10
    [RocciBoard.kicad_pcb, RocciBoard.kicad_sch, bom.csv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]
2024-09-01 cleanup production files
    [BOM-RocciBoard.csv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]
2025-02-28 rework Lochraster for larger pads
    [BOM-Lochraster.csv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]
2025-07-15 added 2S lipo support to the schematic
    [RocciBoard.kicad_sch]
2025-07-15 add xt60 and spereate i2c pwr and data jumper
    [RocciBoard.kicad_pcb, RocciBoard.kicad_sch]
2025-07-24 more progress with nxt shield
    [RocciBoard.kicad_pcb, RocciBoard.kicad_sch, nxt_shield.kicad_pcb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]
2025-09-29 update rocci board to have XT60 and more jumper
    [RocciBoard.kicad_pcb]
2025-09-29 first version of NXT shield with nxt sensors
    [nxt_shield.kicad_pcb, nxt_shield.kicad_sch]
2025-11-08 nxt shield first prototype production
    [RJ12.step, XT60PW MALE.STEP, nxt_shield.kicad_pcb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]
2025-11-08 update rocciboard with thermal release
    [RocciBoard.kicad_pcb]
2026-01-09 Version 1.2 finished
    [LM75900_Lipo_protection_calc.xlsx, RocciBoard.kicad_pcb, RocciBoard.kicad_sch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]

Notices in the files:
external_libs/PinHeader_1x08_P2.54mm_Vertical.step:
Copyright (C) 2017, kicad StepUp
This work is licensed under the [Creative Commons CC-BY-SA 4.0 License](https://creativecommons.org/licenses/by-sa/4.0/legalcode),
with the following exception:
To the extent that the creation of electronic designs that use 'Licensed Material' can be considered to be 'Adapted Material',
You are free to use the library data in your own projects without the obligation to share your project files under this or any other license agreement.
